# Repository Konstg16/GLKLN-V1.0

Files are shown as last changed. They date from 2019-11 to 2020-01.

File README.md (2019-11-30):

# GLKLN-V1.0

<p><h1>Introduction:</h1></p>
<p>This is 3D printer project.</p>
<p>The printer name is GLKLN version 1.0.</p>
<p>The main idea of this printer is to create a new design of a 3D printer with a cubic cartesian scheme which includes as many as possible parts from plastic. I.e. it supports the RepRap concept to create some kind of easy reproducible 3d printer to make it more achievable for a wide engineer society.<br/>
One of the main concepts is that all plastic parts designed to be printed by one hotend 3d printer without using supports.</p>
<p><h1>License:</h1></p>
<p>This work is licensed under the Creative Commons Attribution-ShareAlike 4.0 International License. To view a copy of this license, visit http://creativecommons.org/licenses/by-sa/4.0/ or send a letter to Creative Commons, PO Box 1866, Mountain View, CA 94042, USA.<br/>
<br/>
</p>
<p><h1>Main features:</h1>
1. Cubic construction – Strong and Stable.<br/>
2. Simple construction – The hotbed Z-axes are the part of the construction.<br/>
3. The Hotbed can be increased – up to 240mm x 290mm.<br/>
4. The Z-axis can be increased – up to 310mm.<br/>
5. The belt connection is simple and confident.<br/>
6. Almost all parts of construction made of plastic.</p>
<p><h1>Content:</h1>
1. Overview information file.<br/>
2. Bill of Materials file.<br/>
3. Marlin firmware configured for this model.<br/>
4. STL models of all plastic parts.<br/>
5. Assembly instruction.<br/></p>

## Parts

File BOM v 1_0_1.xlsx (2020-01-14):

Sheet: BOM sum
# | Part definition | Description | PCS
Plastic
1 | Corner LU |  | 1
2 | Corner LU B |  | 1
3 | Corner RU F |  | 1
4 | Corner RU B |  | 1
5 | Corner L |  | 4
6 | Corner B1 |  | 4
7 | Cross |  | 1
8 | wheel holder |  | 2
9 | Motor Holder 1 |  | 2
10 | Front panel |  | 1
11 | Front Train |  | 1
12 | Extruder Flap |  | 2
13 | Cap MkB |  | 1
14 | Back Train |  | 1
15 | Y Train body |  | 1
16 | End Stop holder |  | 6
17 | timing belt holder |  | 6
18 | base plate | Finaly produced from Fiberboard | 1
19 | Side panel |  | 4
20 | Side panel lead |  | 14
21 | Side panel lead Back L |  | 1
22 | Side panel lead Back R |  | 1
23 | Power supply Holder |  | 1
24 | Power supply HolderCap |  | 1
25 | Extruder Holder |  | 1
 |  |  | 60
Profiles
23 | U 20 x 20 x 2 x 400 LU | U shape aluminium profile - Upper frame | 1
24 | U 20 x 20 x 2 x 400 FU | U shape aluminium profile - Upper frame | 1
25 | U 20 x 20 x 2 x 400 RU | U shape aluminium profile - Upper frame | 1
26 | U 20 x 20 x 2 x 400 BU | U shape aluminium profile - Upper frame | 1
27 | U 20 x 20 x 2 x 350 | U shape aluminium profile - Hotbed table | 2
28 | U 20 x 20 x 2 x 248 | U shape aluminium profile - Hotbed table | 4
29 | U 20 x 20 x 2 x 400 L | U shape aluminium profile - Lower frame | 4
 |  |  | 14
Axes
30 | Lin axis 400 x 8 | 8 mm x 400 mm Linear Optical Axis | 6
31 | Lin axis 450 x 8 | 8 mm x 450 mm Linear Optical Axis | 2
32 | Linear rail 6mm x 450mm | 6 mm x 450 mm Linear Optical Axis | 1
 |  |  | 9
Bearing
33 | LM8SUU | LM8SUU linear bearing | 8
34 | LM8UU | LM8UU linear bearing | 4
35 | Bearing 636 zz | Bearing 636 zz ball bearing | 1
 |  |  | 13
Coupling
36 | Shaft Coupling 5 x 6 | Flexible Shaft Coupling 5 x 6 | 1
37 | Shaft Coupling 5 x 8 | Flexible Shaft Coupling 5 x 8 | 2
 |  |  | 3
Motors
38 | 42BYGH40 motor | 42BYGH40 motor | 2
39 | 42BYGH48 motor | 42BYGH48 motor | 2
40 | 42BYGH34 motor | 42BYGH34 motor | 2
41 | Dual Z Stepper Motor Adapter | Dual Z Stepper Motor Adapter | 1
 |  |  | 7
Timing
42 | Timing Wheel T16 W6 ID6 OD13 screw | Timing Wheel T16 W6 ID6 OD13 screw | 2
43 | Timing Wheel T16 W6 ID3 OD13 | Timing Wheel T16 W6 ID3 OD13 | 3
44 | Timing Wheel T16 W6 ID5 OD13 screw | Timing Wheel T16 W6 ID5 OD13 screw | 1
45 | Timing belt T16 W6 | Timing belt GT2 W6 | 2
 |  |  | 8
Fitings
46 | Fitting | Fitting PC4-M6 OD 4mm ID 2mm | 4
47 | 4mm PTFE Tube | 4mm PTFE Tube 2m | 1
 |  |  | 4
Springs
48 | Spring OD8 L27 W0.9 | Spring OD8 L27 W0.9 (Length 20mm) | 2
49 | Spring | Spring 8mm x 25mm | 4
 |  |  | 6
Ventilators
50 | Ventilator 25 x 25 | Ventilator 25 x 25 | 2
51 | Ventilator 40 x 40 | Ventilator 40 x 40 | 1
 |  |  | 3
Extruder
52 | 3D V6 Bowden Extruder Heat Sink | 3D V6 Bowden Extruder Heat Sink | 0
53 | Heater | Heater | 0
54 | nozzel 0.4 | nozzel 0.4 | 0
55 | Throat | Throat | 0
56 | Full complect | V6 Dual Nozzle 2 In 2 Out Double Head with 3010 Fun | 1
 |  |  | 1
Screws
57 | T8 x 300 Screw | T8 x 300 Screw | 2
58 | ISO 7046-1 - M2 x 10 - Z - 10S | M2x10mm - Countersunk flat head cross recess screw | 12
59 | Hex M3 x 25mm Socket Cap Screw | M3 x 25mm - Hex Socket Cap Screw | 12
60 | ISO 4762 M3 x 12 - 12N | M3 x 12mm socket head cap screw | 88
61 | ISO 10642 - M3 x 30 - 30N | M3 x 30mm socket countersunk head screw | 4
62 | ISO 7380 - M3 x 12 - 12N | M3 x 12 - Socket button head screw_iso | 8
63 | Hex M3 x 20mm Socket Cap Screw | Hex M3 x 20mm Socket Cap Screw | 1
64 | ISO 4027 - M3 x 6-C | socket set screw cone point_iso | 8
65 | ISO 7046-1 - M3 x 10 - Z - 10S | countersunk flat head cross recess screw_iso | 2
66 | ISO 4762 M4 x 20 - 20N | socket head cap screw_iso | 2
67 | ISO 4762 M4 x 16 - 16S | socket head cap screw_iso | 2
68 | ISO 4762 M4 x 10 - 10S | socket head cap screw_iso | 2
69 | ISO 7380 - M4 x 12 - 12N | socket button head screw_iso | 60
70 | ISO 4027 - M4 x 8-C | socket set screw cone point_iso | 34
71 | ISO 4027 - M4 x 6-S | socket set screw cone point_iso | 18
 |  |  | 255
Nuts
71 | LMF8UU | LMH8UU | 2
72 | ISO - 4035 - M3 - N | hex thin nut chamfered gradeab_iso | 72
73 | Long Nuts M3 x 30mm | Long Nuts M3 x 30mm | 4
74 | Long Nuts M3 x 25mm | Long Nuts M3 x 25mm | 4
75 | ISO - 4035 - M4 - C | hex thin nut chamfered gradeab M4 iso | 52
 |  |  | 134
Washers
76 | Washer M3 | Washer M3 | 2
 |  |  | 2
Wheels
77 | Guide Wheel Pulley Bearing U604ZZ 4x13x4mm | Guide Wheel Pulley Bearing U604ZZ 4x13x4mm | 2
78 | 26 Tooth Motor Shaft 5mm Gear Wheel | 26 Tooth Motor Shaft 5mm Gear Wheel | 2
 |  |  | 4
Electrical
79 | HotBed Al 220x220x3 | HotBed Al 220x220x3 | 1
80 | PL-08N Level Sensor | PL-08N Level Sensor | 1
81 | EndStopSwitch | EndStopSwitch | 6
82 | MkB PCB | MKS Gen L V1.0 | 1
83 | A4988 | A4988 Stepper Motor Driver With Heat sin | 5
84 | PowerSupply 12V 30A 360A | PowerSupply 12V25A 300W | 1
85 | LCD 2004 screen | LCD 2004 screen | 1
86 | 15A 250V IEC320 C14 3 Pin Fused Power Socket Connector Rocker Switch | 15A 250V IEC320 C14 3 Pin Fused Power Socket Connector Rocker Switch | 1
 |  |  | 17
 |  |  | 540

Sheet: Plastic
# | Part definition | Description | PCS | Time | Total time | Filament length, mm x OD 1,75mm | Total Filament length, mm x OD 1,75mm | Material
1 | Corner LU |  | 1 | 1:59:00 | 1:59:00 | 17076 | 17076 | PLA
2 | Corner LU B |  | 1 | 1:14:00 | 1:14:00 | 10969 | 10969 | PLA
3 | Corner RU F |  | 1 | 1:15:00 | 1:15:00 | 10957 | 10957 | PLA
4 | Corner RU B |  | 1 | 0:39:00 | 0:39:00 | 5578 | 5578 | PLA
5 | Corner L |  | 4 | 0:30:00 | 2:00:00 | 4328 | 17312 | PLA
6 | Corner B1 |  | 4 | 0:45:00 | 3:00:00 | 6641 | 26564 | PLA
7 | Cross |  | 1 | 0:38:00 | 0:38:00 | 5251 | 5251 | PLA
8 | wheel holder |  | 2 | 0:14:00 | 0:28:00 | 2036 | 4072 | PLA
9 | Motor Holder 1 |  | 2 | 0:25:00 | 0:50:00 | 3178 | 6356 | PLA
10 | Front panel |  | 1 | 2:06:00 | 2:06:00 | 16661 | 16661 | PLA
11 | Front Train |  | 1 | 1:47:00 | 1:47:00 | 18369 | 18369 | PLA
12 | Extruder Flap |  | 2 | 0:22:00 | 0:44:00 | 2578 | 5156 | PLA
13 | Cap MkB |  | 1 | 1:06:00 | 1:06:00 | 7484 | 7484 | PLA
14 | Back Train |  | 1 | 2:30:00 | 2:30:00 | 25153 | 25153 | PLA
15 | Y Train body |  | 1 | 1:51:00 | 1:51:00 | 16116 | 16116 | PLA
16 | End Stop holder |  | 6 | 0:08:00 | 0:48:00 | 953 | 5718 | PLA
17 | timing belt holder |  | 6 | 0:06:00 | 0:36:00 | 580 | 3480 | PLA
18 | base plate |  | 1 |  | 0:00:00 |  | 0 | PLA
19 | Side panel |  | 4 | 3:48:00 | 15:12:00 | 31118 | 124472 | PLA
20 | Side panel lead |  | 14 | 0:51:00 | 11:54:00 | 6861 | 96054 | PLA
21 | Side panel lead Back L |  | 1 | 1:13:00 | 1:13:00 | 9732 | 9732 | PLA
22 | Side panel lead Back R |  | 1 | 1:22:00 | 1:22:00 | 10919 | 10919 | PLA
23 | Power supply Holder |  | 1 | 0:34:00 | 0:34:00 | 3623 | 3623 | PLA
24 | Power supply HolderCap |  | 1 | 0:42:00 | 0:42:00 | 5889 | 5889 | PLA
25 | Extruder Holder |  | 1 | 0:26:00 | 0:26:00 | 3175 | 3175 | PLA
 |  |  |  | 2:31:00 | 6:54:00 | 225225 | 456136 | PLA
 | Printing Quality | Layer 0,2mm, filling 60% |  |  |  | Volume, mm^3 | 4388542.614
 | Host SW | Repetier Host |  |  |  | Density, kg/mm^3 | 1.24e-06
 | Sliser | CuraEmgine |  |  |  | Mass, kg | 5.4
 |  |  |  |  |  | *According to my experience the real required mateerial mass is about 2,5kg

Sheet: Profile
# | Part definition | Description | PCS
23 | U 20 x 20 x 2 x 400 LU | U shape aluminium profile - Upper frame | 1
24 | U 20 x 20 x 2 x 400 FU | U shape aluminium profile - Upper frame | 1
25 | U 20 x 20 x 2 x 400 RU | U shape aluminium profile - Upper frame | 1
26 | U 20 x 20 x 2 x 400 BU | U shape aluminium profile - Upper frame | 1
27 | U 20 x 20 x 2 x 350 | U shape aluminium profile - Hotbed table | 2
28 | U 20 x 20 x 2 x 248 | U shape aluminium profile - Hotbed table | 4
29 | U 20 x 20 x 2 x 400 L | U shape aluminium profile - Lower frame | 4

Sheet: Axes
# | Part definition | Description | PCS
30 | Lin axis 400 x 8 | 8 mm x 400 mm Linear Optical Axis | 6
31 | Lin axis 450 x 8 | 8 mm x 450 mm Linear Optical Axis | 2
32 | Linear rail 6mm x 450mm | 6 mm x 450 mm Linear Optical Axis | 1

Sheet: Bearing
# | Part definition | Description | PCS
33 | LM8SUU | LM8SUU linear bearing | 8
34 | LM8UU | LM8UU linear bearing | 4
35 | Bearing 636 zz | Bearing 636 zz ball bearing | 1

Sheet: Coupling
# | Part definition | Description | PCS
36 | Shaft Coupling 5 x 6 | Flexible Shaft Coupling 5 x 6 | 1
37 | Shaft Coupling 5 x 8 | Flexible Shaft Coupling 5 x 8 | 2

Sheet: Motors
# | Part definition | Description | PCS
38 | 42BYGH40 motor | 42BYGH40 motor | 2
39 | 42BYGH48 motor | 42BYGH48 motor | 2
40 | 42BYGH34 motor | 42BYGH34 motor | 2
41 | Dual Z Stepper Motor Adapter | Dual Z Stepper Motor Adapter | 1

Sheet: Timing
# | Part definition | Description | PCS
42 | Timing Wheel T16 W6 ID6 OD13 screw | Timing Wheel T16 W6 ID6 OD13 screw | 2
43 | Timing Wheel T16 W6 ID3 OD13 | Timing Wheel T16 W6 ID3 OD13 | 3
44 | Timing Wheel T16 W6 ID5 OD13 screw | Timing Wheel T16 W6 ID5 OD13 screw | 1
45 | Timing belt T16 W6 | Timing belt GT2 W6 | 2

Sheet: Fitings
# | Part definition | Description | PCS
46 | Fitting | Fitting PC4-M6 OD 4mm ID 2mm | 4
47 | 4mm PTFE Tube | 4mm PTFE Tube 2m | 1

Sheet: Springs
# | Part definition | Description | PCS
48 | Spring OD8 L27 W0.9 | Spring OD8 L27 W0.9 (Length 20mm) | 2
49 | Spring | Spring 8mm x 25mm | 4

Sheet: Ventilators
# | Part definition | Description | PCS
50 | Ventilator 25 x 25 | Ventilator 25 x 25 | 2
51 | Ventilator 40 x 40 | Ventilator 40 x 40 | 1

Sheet: Extruder
# | Part definition | Description | PCS
56 | Full complect | V6 Dual Nozzle 2 In 2 Out Double Head with 3010 Fun | 1

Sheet: Screw
# | Part definition | Description | PCS
57 | T8 x 300 Screw | T8 x 300 Screw | 2
58 | ISO 7046-1 - M2 x 10 - Z - 10S | M2x10mm - Countersunk flat head cross recess screw | 12
59 | Hex M3 x 25mm Socket Cap Screw | M3 x 25mm - Hex Socket Cap Screw | 12
60 | ISO 4762 M3 x 12 - 12N | M3 x 12mm socket head cap screw | 88
61 | ISO 10642 - M3 x 30 - 30N | M3 x 30mm socket countersunk head screw | 4
62 | ISO 7380 - M3 x 12 - 12N | M3 x 12 - Socket button head screw_iso | 8
63 | Hex M3 x 20mm Socket Cap Screw | Hex M3 x 20mm Socket Cap Screw | 1
64 | ISO 4027 - M3 x 6-C | socket set screw cone point_iso | 8
65 | ISO 7046-1 - M3 x 10 - Z - 10S | countersunk flat head cross recess screw_iso | 2
66 | ISO 4762 M4 x 20 - 20N | socket head cap screw_iso | 2
67 | ISO 4762 M4 x 16 - 16S | socket head cap screw_iso | 2
68 | ISO 4762 M4 x 10 - 10S | socket head cap screw_iso | 2
69 | ISO 7380 - M4 x 12 - 12N | socket button head screw_iso | 60
70 | ISO 4027 - M4 x 8-C | socket set screw cone point_iso | 34
71 | ISO 4027 - M4 x 6-S | socket set screw cone point_iso | 18

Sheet: Nuts
# | Part definition | Description | PCS
71 | LMF8UU | LMH8UU | 2
72 | ISO - 4035 - M3 - N | hex thin nut chamfered gradeab_iso | 72
73 | Long Nuts M3 x 30mm | Long Nuts M3 x 30mm | 4
74 | Long Nuts M3 x 25mm | Long Nuts M3 x 25mm | 4
75 | ISO - 4035 - M4 - C | hex thin nut chamfered gradeab M4 iso | 52

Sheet: Washers
# | Part definition | Description | PCS
76 | Washer M3 | Washer M3 | 2

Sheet: Wheels
# | Part definition | Description | PCS
77 | Guide Wheel Pulley Bearing U604ZZ 4x13x4mm | Guide Wheel Pulley Bearing U604ZZ 4x13x4mm | 2
78 | 26 Tooth Motor Shaft 5mm Gear Wheel | 26 Tooth Motor Shaft 5mm Gear Wheel | 2

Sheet: Electrical
# | Part definition | Description | PCS
79 | HotBed Al 220x220x3 | HotBed Al 220x220x3 | 1
80 | PL-08N Level Sensor | PL-08N Level Sensor | 1
81 | EndStopSwitch | EndStopSwitch | 6
82 | MkB PCB | MKS Gen L V1.0 | 1
83 | A4988 | A4988 Stepper Motor Driver With Heat sin | 5
84 | PowerSupply 12V 30A 360A | PowerSupply 12V25A 300W | 1
85 | LCD 2004 screen | LCD 2004 screen | 1
86 | 15A 250V IEC320 C14 3 Pin Fused Power Socket Connector Rocker Switch | 15A 250V IEC320 C14 3 Pin Fused Power Socket Connector Rocker Switch | 1

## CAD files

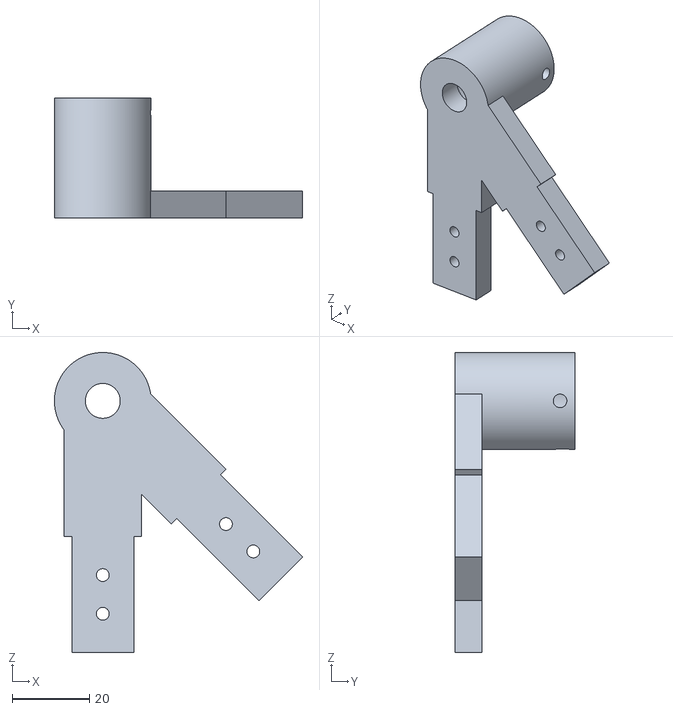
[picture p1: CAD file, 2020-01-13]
STLModels/Corner B1.STL
64.1 x 31.0 x 77.5

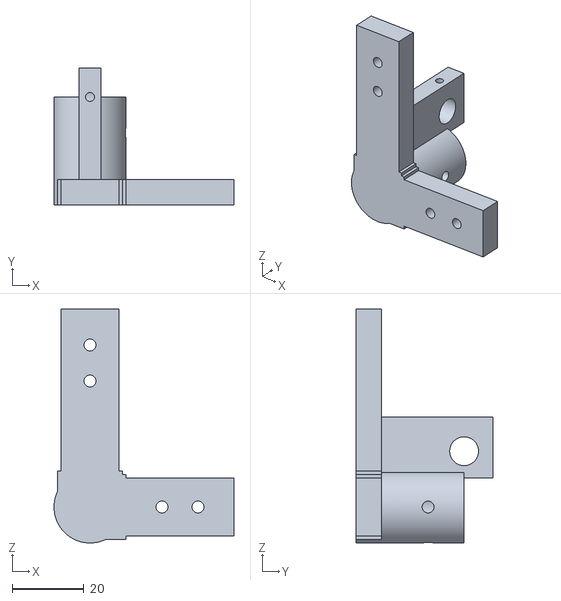
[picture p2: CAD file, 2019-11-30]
STLModels/Corner RU B.STL
50.0 x 38.0 x 65.0

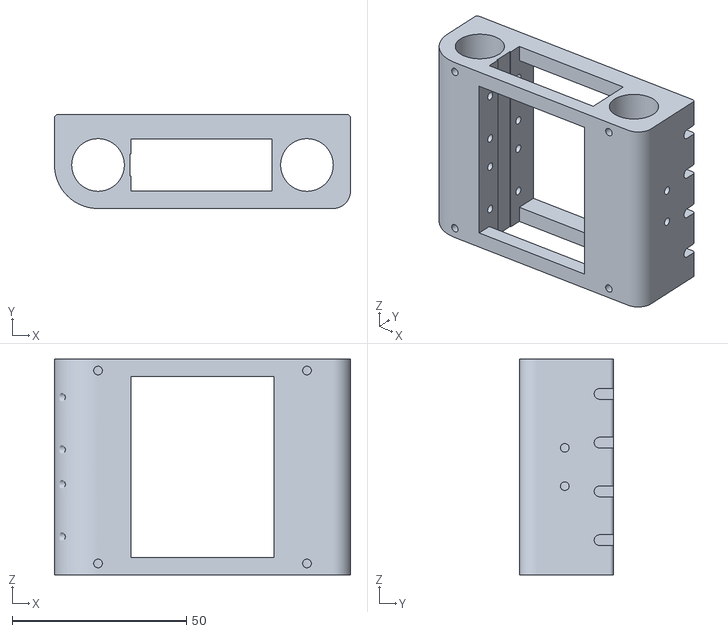
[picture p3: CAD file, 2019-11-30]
STLModels/Y Train body.STL
85.0 x 27.0 x 62.0

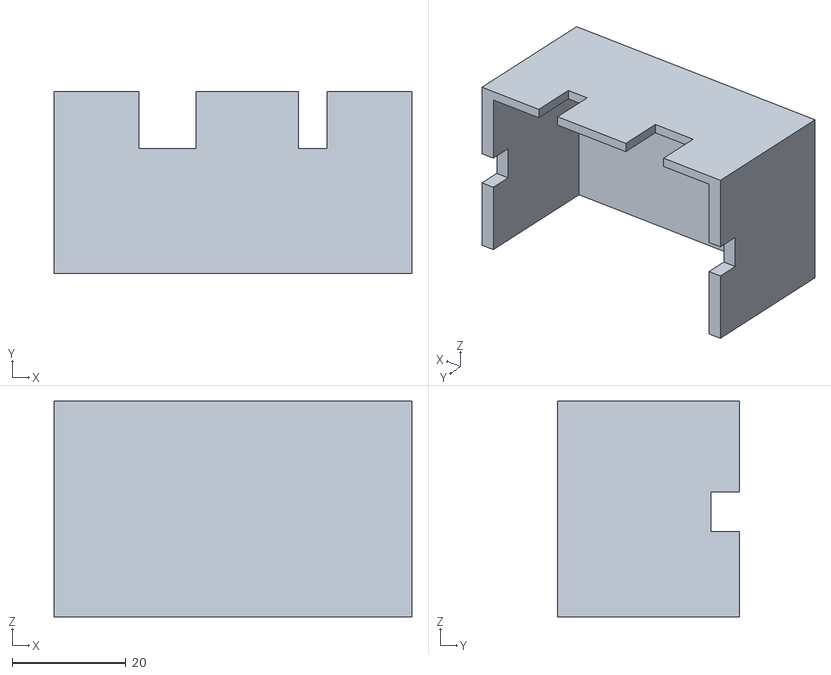
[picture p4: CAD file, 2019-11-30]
STLModels/PowerSupplayHolderCap.STL
63.0 x 32.0 x 38.0

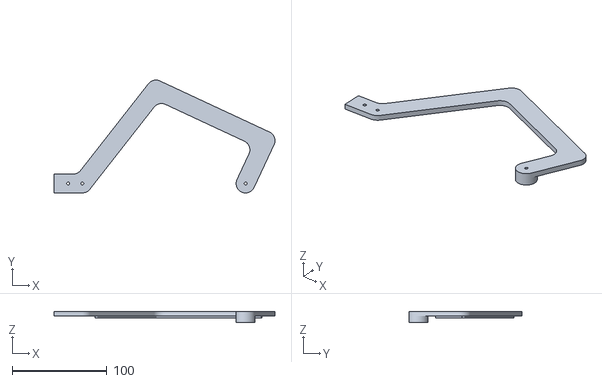
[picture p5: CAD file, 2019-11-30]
STLModels/Side Panel Lead Back R.STL
233.7 x 119.4 x 12.0

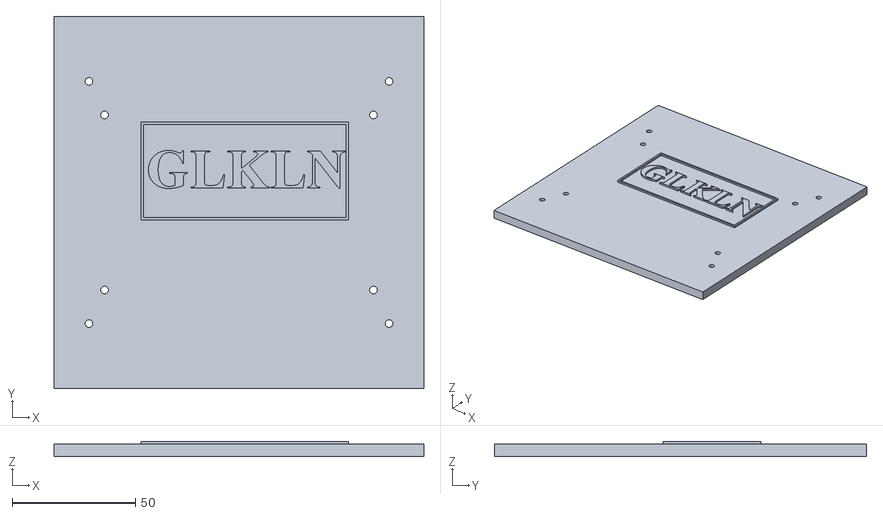
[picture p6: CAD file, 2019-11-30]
STLModels/Side Panel.STL
150.0 x 151.0 x 6.00

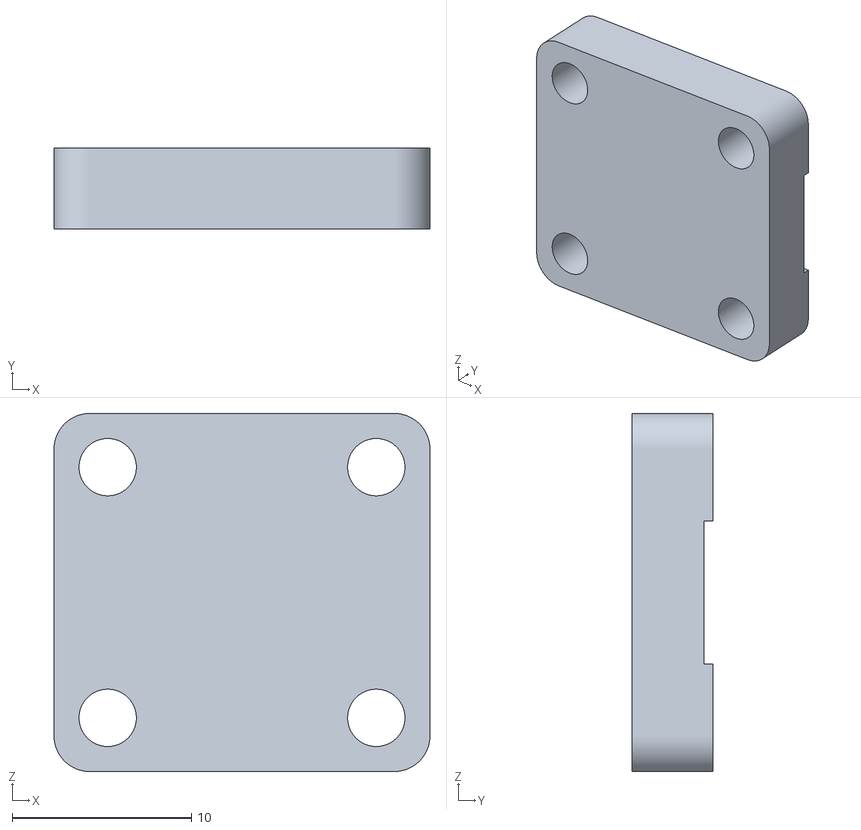
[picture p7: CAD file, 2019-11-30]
STLModels/timing belt holder.STL
21.0 x 4.50 x 20.0

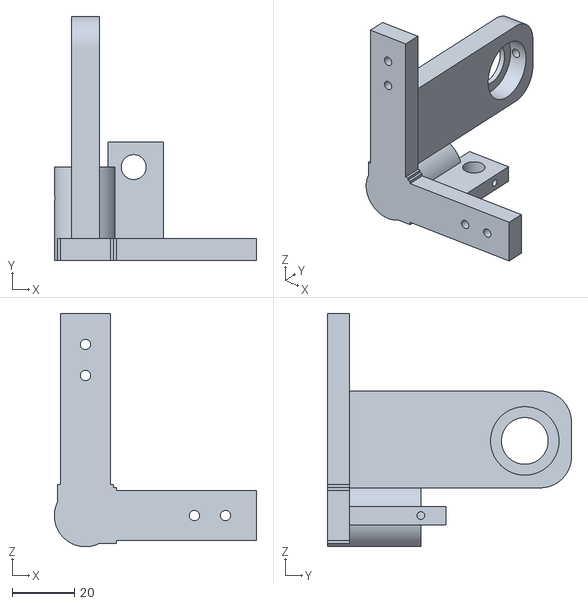
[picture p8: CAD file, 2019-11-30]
STLModels/Corner LU B.STL
65.0 x 78.4 x 75.0

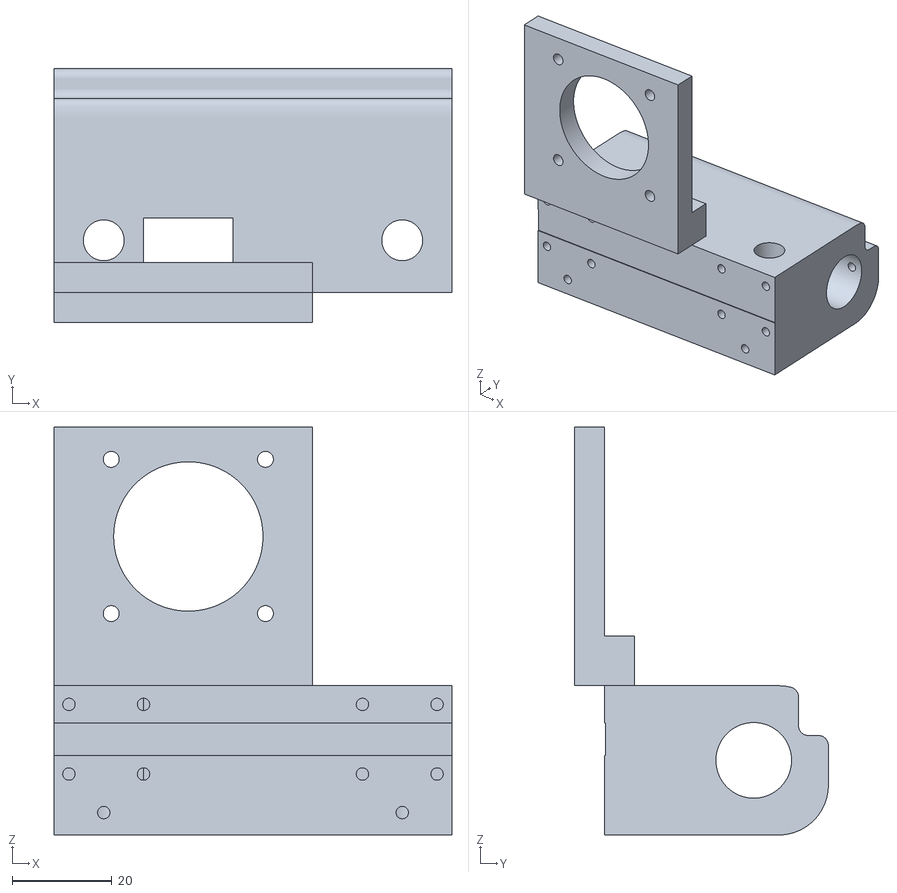
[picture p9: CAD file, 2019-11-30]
STLModels/Back Train.STL
80.0 x 51.0 x 82.0

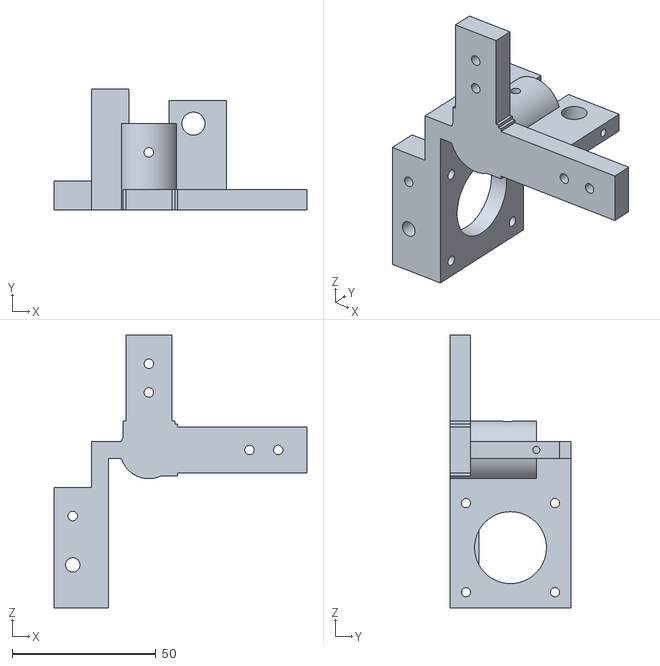
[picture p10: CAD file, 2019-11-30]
STLModels/Corner RU F.STL
88.0 x 42.0 x 95.0

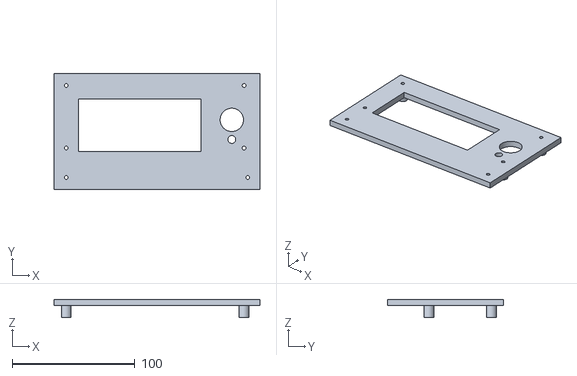
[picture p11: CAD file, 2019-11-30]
STLModels/Front panel.STL
168.0 x 95.0 x 15.0

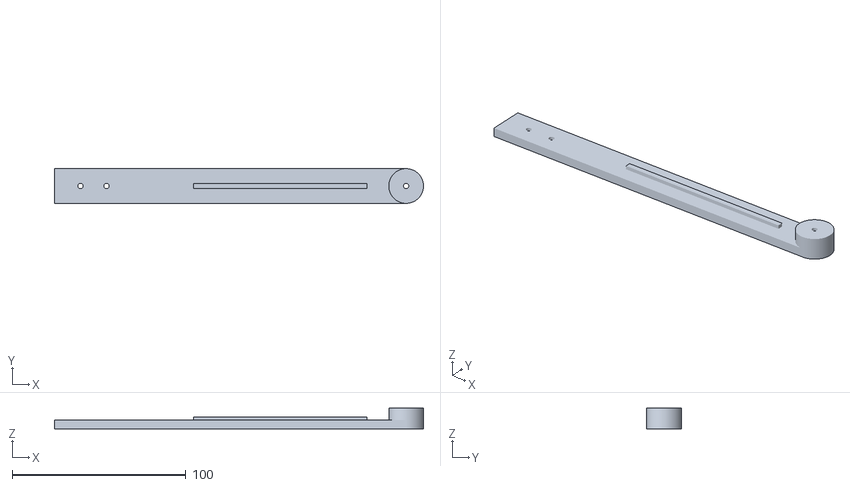
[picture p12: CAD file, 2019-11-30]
STLModels/Side Panel Lead.STL
212.6 x 20.0 x 12.0

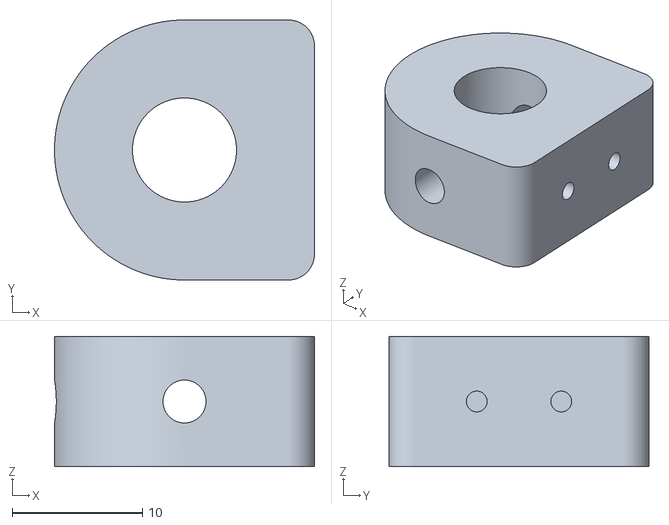
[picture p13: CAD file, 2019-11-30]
STLModels/End Stop holder.STL
20.0 x 20.0 x 10.0

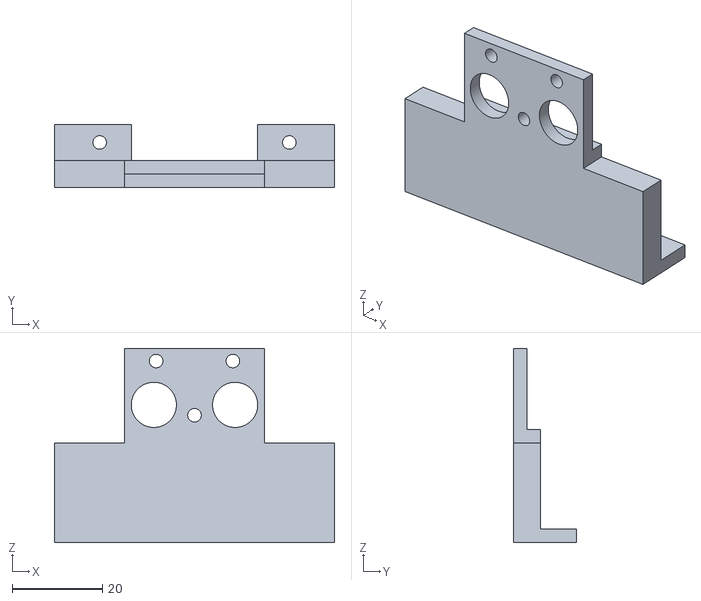
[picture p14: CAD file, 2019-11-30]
STLModels/ExtruderHolder.STL
62.0 x 14.0 x 43.0

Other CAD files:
STLModels/Extruder Flap.STL
STLModels/Motor Holder 1.STL
STLModels/Corner L.STL
STLModels/PowerSupplayHolder.STL
STLModels/Cap MkB.STL
STLModels/Corner LU.STL
STLModels/Cross.STL
STLModels/Front Train.STL
STLModels/Side Panel Lead Back L.STL
STLModels/wheel holder.STL

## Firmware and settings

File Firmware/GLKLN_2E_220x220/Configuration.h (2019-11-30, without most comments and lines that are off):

#define CONFIGURATION_H
#define CONFIGURATION_H_VERSION 010109
#define STRING_CONFIG_H_AUTHOR "Konstantin Goulitski" // Who made the changes.
#define SHOW_BOOTSCREEN
#define STRING_SPLASH_LINE1 SHORT_BUILD_VERSION // will be shown during bootup in line 1
#define STRING_SPLASH_LINE2 WEBSITE_URL         // will be shown during bootup in line 2
#define SERIAL_PORT 0
#define BAUDRATE 250000
  #define MOTHERBOARD BOARD_MKS_GEN_L
#define CUSTOM_MACHINE_NAME "GLKLN_v1.0"
#define EXTRUDERS 2
#define DEFAULT_NOMINAL_FILAMENT_DIA 1.75
#define HOTEND_OFFSET_X {0.0, 0.00} // (in mm) for each extruder, offset of the hotend on the X axis
#define HOTEND_OFFSET_Y {0.0, 17.50}  // (in mm) for each extruder, offset of the hotend on the Y axis
#define POWER_SUPPLY 0
#define TEMP_SENSOR_0 1
#define TEMP_SENSOR_1 1
#define TEMP_SENSOR_2 0
#define TEMP_SENSOR_3 0
#define TEMP_SENSOR_4 0
#define TEMP_SENSOR_BED 11
#define TEMP_SENSOR_CHAMBER 0
#define DUMMY_THERMISTOR_998_VALUE 25
#define DUMMY_THERMISTOR_999_VALUE 100
#define MAX_REDUNDANT_TEMP_SENSOR_DIFF 10
#define TEMP_RESIDENCY_TIME 10  // (seconds)
#define TEMP_HYSTERESIS 3       // (degC) range of +/- temperatures considered "close" to the target one
#define TEMP_WINDOW     1       // (degC) Window around target to start the residency timer x degC early.
#define TEMP_BED_RESIDENCY_TIME 10  // (seconds)
#define TEMP_BED_HYSTERESIS 3       // (degC) range of +/- temperatures considered "close" to the target one
#define TEMP_BED_WINDOW     1       // (degC) Window around target to start the residency timer x degC early.
#define HEATER_0_MINTEMP 5
#define HEATER_1_MINTEMP 5
#define HEATER_2_MINTEMP 5
#define HEATER_3_MINTEMP 5
#define HEATER_4_MINTEMP 5
#define BED_MINTEMP 5
#define HEATER_0_MAXTEMP 275
#define HEATER_1_MAXTEMP 275
#define HEATER_2_MAXTEMP 275
#define HEATER_3_MAXTEMP 275
#define HEATER_4_MAXTEMP 275
#define BED_MAXTEMP 150
#define PIDTEMP
#define BANG_MAX 255     // Limits current to nozzle while in bang-bang mode; 255=full current
#define PID_MAX BANG_MAX // Limits current to nozzle while PID is active (see PID_FUNCTIONAL_RANGE below); 255=full current
#define PID_K1 0.95      // Smoothing factor within any PID loop
  #define PID_FUNCTIONAL_RANGE 10 // If the temperature difference between the target temperature and the actual temperature
  #define DEFAULT_Kp 22.2
  #define DEFAULT_Ki 1.08
  #define DEFAULT_Kd 114
#define MAX_BED_POWER 255 // limits duty cycle to bed; 255=full current
#define PREVENT_COLD_EXTRUSION
#define EXTRUDE_MINTEMP 170
#define PREVENT_LENGTHY_EXTRUDE
#define EXTRUDE_MAXLENGTH 200
#define THERMAL_PROTECTION_HOTENDS // Enable thermal protection for all extruders
#define USE_XMIN_PLUG
#define USE_YMIN_PLUG
#define USE_ZMIN_PLUG
#define USE_XMAX_PLUG
#define USE_YMAX_PLUG
#define USE_ZMAX_PLUG
#define ENDSTOPPULLUPS
#define X_MIN_ENDSTOP_INVERTING true // set to true to invert the logic of the endstop.
#define Y_MIN_ENDSTOP_INVERTING true // set to true to invert the logic of the endstop.
#define Z_MIN_ENDSTOP_INVERTING true // set to true to invert the logic of the endstop.
#define X_MAX_ENDSTOP_INVERTING true // set to true to invert the logic of the endstop.
#define Y_MAX_ENDSTOP_INVERTING true // set to true to invert the logic of the endstop.
#define Z_MAX_ENDSTOP_INVERTING true // set to true to invert the logic of the endstop.
#define Z_MIN_PROBE_ENDSTOP_INVERTING true // set to true to invert the logic of the probe.
#define X_DRIVER_TYPE  A4988
#define Y_DRIVER_TYPE  A4988
#define Z_DRIVER_TYPE  A4988
#define X2_DRIVER_TYPE A4988
#define Y2_DRIVER_TYPE A4988
#define Z2_DRIVER_TYPE A4988
#define E0_DRIVER_TYPE A4988
#define E1_DRIVER_TYPE A4988
#define DEFAULT_AXIS_STEPS_PER_UNIT   { 100, 100, 396.82, 94}
#define DEFAULT_MAX_FEEDRATE          { 300, 300, 1.5, 25 }
#define DEFAULT_MAX_ACCELERATION      { 1000, 1000, 50, 10000 }
#define DEFAULT_ACCELERATION          200    // X, Y, Z and E acceleration for printing moves
#define DEFAULT_RETRACT_ACCELERATION  3000    // E acceleration for retracts
#define DEFAULT_TRAVEL_ACCELERATION   3000    // X, Y, Z acceleration for travel (non printing) moves
#define DEFAULT_XJERK                 15.0
#define DEFAULT_YJERK                 15.0
#define DEFAULT_ZJERK                  0.4
#define DEFAULT_EJERK                  5.0
#define Z_MIN_PROBE_USES_Z_MIN_ENDSTOP_PIN
#define FIX_MOUNTED_PROBE
#define X_PROBE_OFFSET_FROM_EXTRUDER 38  // X offset: -left  +right  [of the nozzle]
#define Y_PROBE_OFFSET_FROM_EXTRUDER -9  // Y offset: -front +behind [the nozzle]
#define Z_PROBE_OFFSET_FROM_EXTRUDER 1   // Z offset: -below +above  [the nozzle]
#define MIN_PROBE_EDGE 10
#define XY_PROBE_SPEED 8000
#define Z_PROBE_SPEED_FAST HOMING_FEEDRATE_Z
#define Z_PROBE_SPEED_SLOW (Z_PROBE_SPEED_FAST / 2)
#define Z_CLEARANCE_DEPLOY_PROBE   10 // Z Clearance for Deploy/Stow
#define Z_CLEARANCE_BETWEEN_PROBES  5 // Z Clearance between probe points
#define Z_CLEARANCE_MULTI_PROBE     5 // Z Clearance between multiple probes
#define Z_PROBE_LOW_POINT          -4 // Farthest distance below the trigger-point to go before stopping
#define Z_PROBE_OFFSET_RANGE_MIN -20
#define Z_PROBE_OFFSET_RANGE_MAX 20
#define X_ENABLE_ON 0
#define Y_ENABLE_ON 0
#define Z_ENABLE_ON 0
#define E_ENABLE_ON 0 // For all extruders
#define DISABLE_X false
#define DISABLE_Y false
#define DISABLE_Z false
#define DISABLE_E false // For all extruders
#define DISABLE_INACTIVE_EXTRUDER true // Keep only the active extruder enabled.
#define INVERT_X_DIR false
#define INVERT_Y_DIR false
#define INVERT_Z_DIR false
#define INVERT_E0_DIR true
#define INVERT_E1_DIR false
#define INVERT_E2_DIR false
#define INVERT_E3_DIR false
#define INVERT_E4_DIR false
#define Z_HOMING_HEIGHT 4  // (in mm) Minimal z height before homing (G28) for Z clearance above the bed, clamps, ...
#define X_HOME_DIR -1
#define Y_HOME_DIR -1
#define Z_HOME_DIR -1
#define X_BED_SIZE 220
#define Y_BED_SIZE 220
#define X_MIN_POS 0
#define Y_MIN_POS 0
#define Z_MIN_POS 0
#define X_MAX_POS X_BED_SIZE
#define Y_MAX_POS Y_BED_SIZE
#define Z_MAX_POS 200
#define MIN_SOFTWARE_ENDSTOPS
  #define MIN_SOFTWARE_ENDSTOP_X
  #define MIN_SOFTWARE_ENDSTOP_Y
  #define MIN_SOFTWARE_ENDSTOP_Z
#define MAX_SOFTWARE_ENDSTOPS
  #define MAX_SOFTWARE_ENDSTOP_X
  #define MAX_SOFTWARE_ENDSTOP_Y
  #define MAX_SOFTWARE_ENDSTOP_Z
#define MESH_BED_LEVELING
#define RESTORE_LEVELING_AFTER_G28
  #define ENABLE_LEVELING_FADE_HEIGHT
  #define SEGMENT_LEVELED_MOVES
  #define LEVELED_SEGMENT_LENGTH 5.0 // (mm) Length of all segments (except the last one)
  #define MESH_INSET 10          // Set Mesh bounds as an inset region of the bed
  #define GRID_MAX_POINTS_X 3    // Don't use more than 7 points per axis, implementation limited.
  #define GRID_MAX_POINTS_Y GRID_MAX_POINTS_X
#define LCD_BED_LEVELING
  #define MBL_Z_STEP 0.025    // Step size while manually probing Z axis.
  #define LCD_PROBE_Z_RANGE 6 // Z Range centered on Z_MIN_POS for LCD Z adjustment
#define MANUAL_X_HOME_POS -25
#define MANUAL_Y_HOME_POS -50
#define Z_SAFE_HOMING
  #define Z_SAFE_HOMING_X_POINT ((X_BED_SIZE) / 2)    // X point for Z homing when homing all axes (G28).
  #define Z_SAFE_HOMING_Y_POINT ((Y_BED_SIZE) / 2)    // Y point for Z homing when homing all axes (G28).
#define HOMING_FEEDRATE_XY (50*60)
#define HOMING_FEEDRATE_Z  (4*60)
#define EEPROM_SETTINGS // Enable for M500 and M501 commands
#define EEPROM_CHITCHAT   // Give feedback on EEPROM commands. Disable to save PROGMEM.
#define HOST_KEEPALIVE_FEATURE        // Disable this if your host doesn't like keepalive messages
#define DEFAULT_KEEPALIVE_INTERVAL 2  // Number of seconds between "busy" messages. Set with M113.
#define BUSY_WHILE_HEATING            // Some hosts require "busy" messages even during heating
#define PREHEAT_1_TEMP_HOTEND 190
#define PREHEAT_1_TEMP_BED     40
#define PREHEAT_1_FAN_SPEED     0 // Value from 0 to 255
#define PREHEAT_2_TEMP_HOTEND 230
#define PREHEAT_2_TEMP_BED    100
#define PREHEAT_2_FAN_SPEED     0 // Value from 0 to 255
#define PRINTJOB_TIMER_AUTOSTART
#define LCD_LANGUAGE en
#define DISPLAY_CHARSET_HD44780 JAPANESE
#define SDSUPPORT
#define SPEAKER
#define REPRAP_DISCOUNT_SMART_CONTROLLER
#define SOFT_PWM_SCALE 0
#define NUM_SERVOS 1 // Servo index starts with 0 for M280 command
#define SERVO_DELAY { 300 }

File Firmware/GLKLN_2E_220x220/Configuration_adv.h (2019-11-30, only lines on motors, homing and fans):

#define E0_AUTO_FAN_PIN -1
#define E1_AUTO_FAN_PIN -1
#define E2_AUTO_FAN_PIN -1
#define E3_AUTO_FAN_PIN -1
#define E4_AUTO_FAN_PIN -1
#define CHAMBER_AUTO_FAN_PIN -1
#define X_HOME_BUMP_MM 5
#define Y_HOME_BUMP_MM 5
#define Z_HOME_BUMP_MM 2
#define HOMING_BUMP_DIVISOR { 2, 2, 4 }  // Re-Bump Speed Divisor (Divides the Homing Feedrate)
#define MICROSTEP_MODES { 16, 16, 16, 16, 16 } // [1,2,4,8,16]
#define DIGIPOT_I2C_MOTOR_CURRENTS { 1.0, 1.0, 1.0, 1.0, 1.0, 1.0, 1.0, 1.0 }  //  AZTEEG_X3_PRO

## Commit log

2019-11-30 Added BOM file
    [BOM v 1_0_1.xlsx]
2019-11-30 Added Firmware
    [Configuration.h, Configuration_adv.h]
2019-11-30 Added STL models
    [BOM v 1_0_1.xlsx, Back Train.STL, Cap MkB.STL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]
2019-12-01 BOM update & Add Description Word file
    [BOM v 1_0_1.xlsx]
2020-01-13 apdate description
    acomplished the description with the additional information about assembly
    [BOM v 1_0_1.xlsx, Corner B1.STL]
2020-01-14 Update BOM v 1_0_1.xlsx
    [BOM v 1_0_1.xlsx]

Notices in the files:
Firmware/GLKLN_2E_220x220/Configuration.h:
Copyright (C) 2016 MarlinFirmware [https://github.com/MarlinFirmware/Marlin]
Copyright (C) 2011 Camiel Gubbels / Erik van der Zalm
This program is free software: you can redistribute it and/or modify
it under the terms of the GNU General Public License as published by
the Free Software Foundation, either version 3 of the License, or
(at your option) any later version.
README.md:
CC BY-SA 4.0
